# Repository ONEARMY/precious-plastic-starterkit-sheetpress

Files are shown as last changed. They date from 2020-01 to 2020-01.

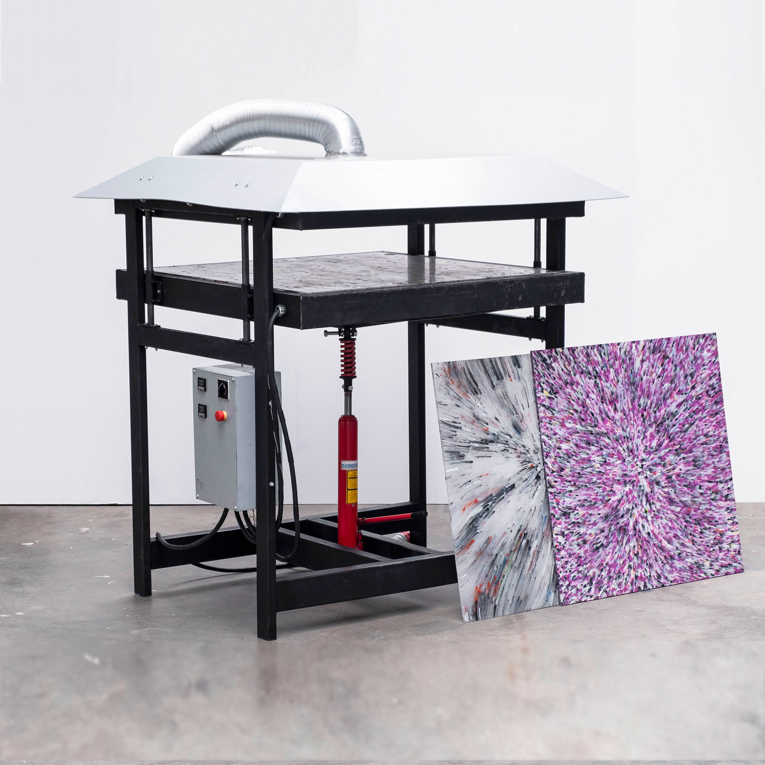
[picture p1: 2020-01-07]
3. Build the machine/Sheetpress-image.jpg

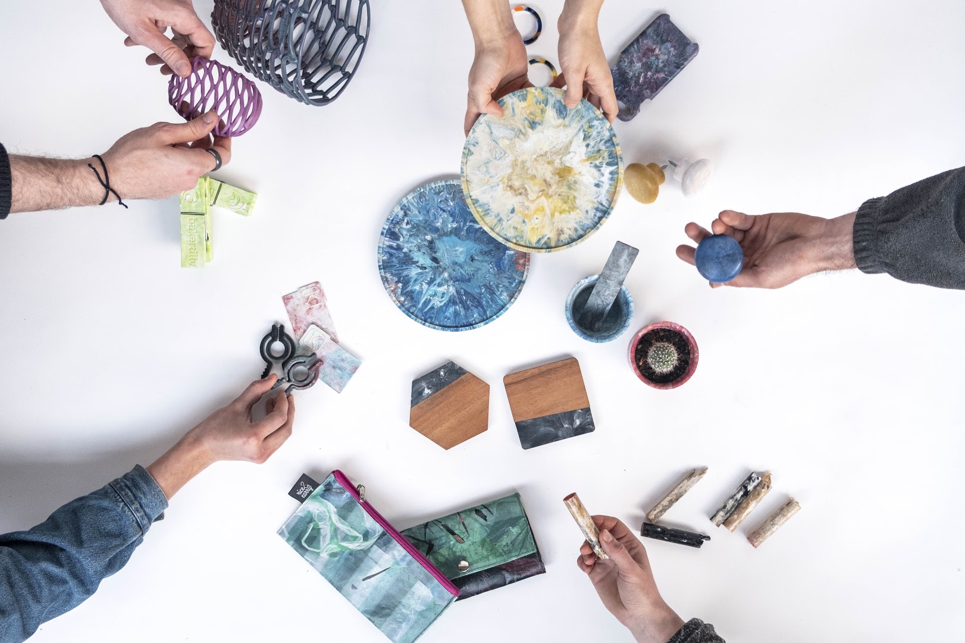
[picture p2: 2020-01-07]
6. Run your Workspace/3. Share/2. Project Images/Products/Products.jpg

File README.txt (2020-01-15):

# Starterkit - Sheetpress Workspace V1.1

YEAH, you made it into a starter-kit!
Start with the 0. Start folder.. read the introduction text and make sure to watch the videos from our website.

If you have any questions visit our community platform or Discord
https://community.preciousplastic.com/
https://discordapp.com/invite/rnx7m4t

Good luck!!

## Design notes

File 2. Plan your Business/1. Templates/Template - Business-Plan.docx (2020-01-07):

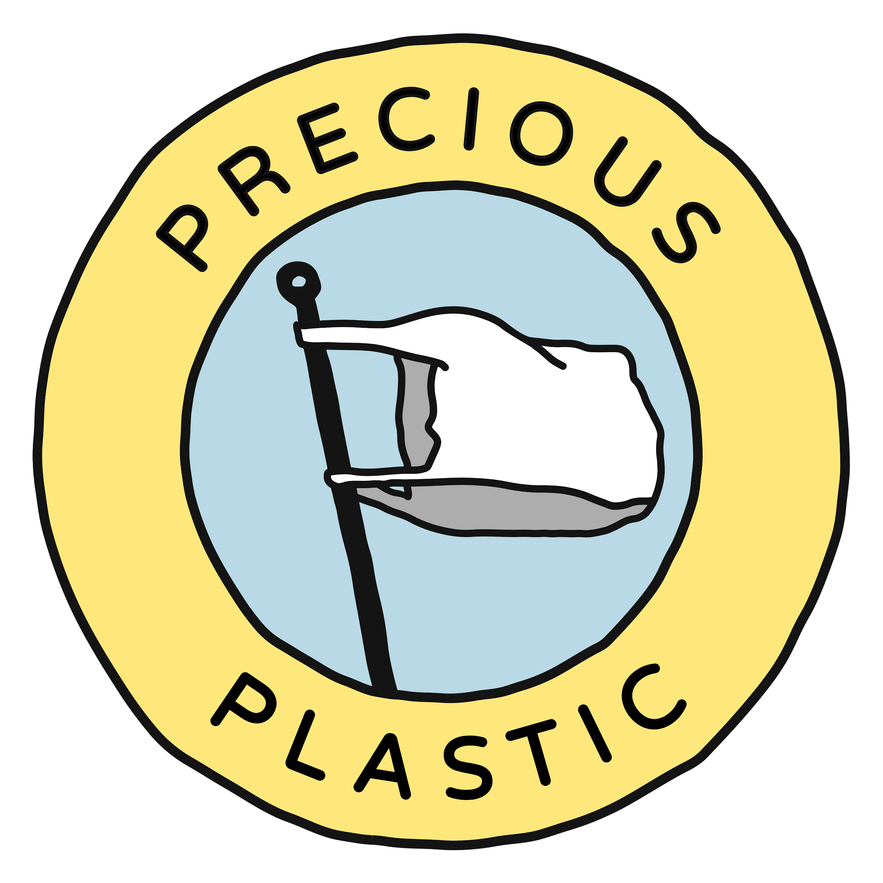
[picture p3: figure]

Your Logo and Business Name Here 👆

# Contact Details

Contact name:

Address:

City:

Zip:

Email:

Phone Number:

Website URL :

# Outline

1. Executive summary
2. Mission
3. Team
4. Market Analysis
  a. Product and Services
  b. Target Groups
  c. Engagement
  d. Sales Channels
5. Operations
  a. Key Resources
  b. Key Activities
  c. Running Costs
  d. Collaborators
6. Impact Measures
  a. Community
  b. Planet
  c. Income Streams
7. Financials
8. Legal Structure
9. Appendix

# 1. Executive Summary

This is your chance to quickly make your argument of what the problem is and how your business is going to solve it. This section shouldn’t be more than a couple paragraphs. Quickly cover the problem, your unique solution, who you’re targeting, and what your impact will be. It’s best to write this section after you’ve completed the whole business plan.

# 2. Mission

What’s the problem?

It’s best to start off describing what problem you’re solving. If your audience might need some education about the plastic waste problem - here’s your chance. What part or aspect of the plastic waste problem are you focusing on? You can set some context about the global plastic waste issue, but make sure to drill down to your national and local level as well. Try to be specific and stress why this is such a big problem facing the planet and your local community. Show your passion for solving this problem. This section will set the stage for the whole story told throughout the plan.

What’s your solution?

Next briefly cover how your solution addresses this problem. For example, if you write about how the plastic waste problem is due to a lifestyle issue, maybe you’re solution is focused on educating people because it addresses the root cause of the problem.

What’s your mission statement?

Look back on your mission that you filled out in the action plan. How can you elaborate to explain it to your reader?

What’s your vision?

Once you have explained your mission - write just a few sentences about your vision. What kind of world do you envision, and what do you envision for your organization?

# 3. Team

Fill in some basic information about your team to show who’s involved and what relevant skills and experience they have to the business.

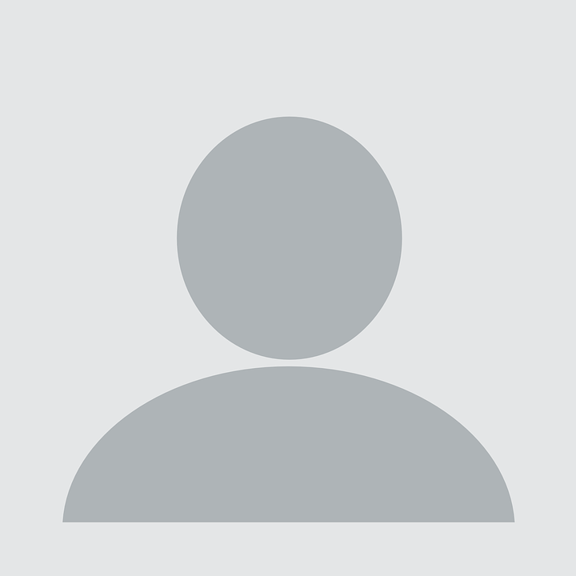
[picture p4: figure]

Name: Role: Experience: | Name: Role: Experience: | Name: Role: Experience:

# 4. Market Analysis

The market analysis section (broken down by the right side of the action plan), is where you will describe how the market is currently performing in your area of interest, how you plan to enter the market, what makes you different, who you are targeting, and how you will deliver your products and services to the customer.

## A. Products & Services

Product explanation

Explain that there is something missing from the market currently and what unique products or services you will offer to meet that unmet need. Write down a brief description of the products and services you are planning to make and include some pictures if possible. Include the price range they will be in and how this compares to similar products/services. If you have any sketches or pictures of your products, you can also include them here.

Product Photos or Sketches:

Competitive advantage

It’s unlikely that your product or service is completely unique - there are businesses or organizations that are probably doing something similar. What are those businesses, what are they offering, and how are you differentiating yourself? Another way to ask this what is your competitive advantage? What are you doing that sets you apart? Describe it here.

Total Available Market

What would you estimate to be the total available market for your product or service? For example, I’m targeting the plastic waste generated in my town, and I know from my city waste department that we generate about 100 tons per month of waste plastic. That means if we were to capture 100 % of the market, we would be processing all 100 tons. If we value each ton at $10, that a $12,000 total available market per year. You should include the total available market that you’re targeting to show how big your business could potentially grow.

## B. Target Groups

Identify the groups

In this section, explain who your target customer groups are, and how many potential customers are in this group. What do you know about these groups? This is your chance to communicate your research about your customers.

Research

What research have you done to show that your target groups will be interested in your products and services? Discuss any field research that you’ve done or online research about these groups. For example, if you’re producing craft furniture from plastic waste, do some research online to see if you can find numbers on the total craft furniture market value in your country. You could also run a small survey in your area to gauge interest in your products.

If you’re targeting businesses, do you have any letters of intent or proof that they are willing to buy your product or service when you’re able to get up and running? This can be a very powerful tool for showing your business case - you already have customers lining up to buy.

## C. Engagement

Engagement is how you will engage with your target customer groups and how many people you can potentially reach with this engagement strategy. What marketing channels are you using? If you’re using social media - which platforms? What’s your engagement rollout plan? Do you intend to start with one marketing channel and then gradually expand? Communicate your marketing plan here.

## D. Sales Channels

Finally, explain what your sales channels are. Explain where and how people can buy your products/services. Explain why you chose these sales channels, and relate that back to your target groups.

Business to Business (B to B) versus Business to Consumer (B to C)

Are you focusing on business to consumer or business to business? This is an important distinction, because it will help the reader understand your business model. Business to consumer (B to C) means that you are targeting consumers directly - you will be the one selling the product or service to the end user. If you are instead focusing on business to business (B to B), that means that you’ll be selling to other businesses. For example - if you’re a machine builder that will be selling machines to new workspaces - this is a business to business model. If you are a product producer selling products directly to people through the Precious Plastic Bazar, this is an example of business to consumer.

# 5. Operations

## A. Key Resources

First explain what key resources, or the key tools, machines, people, and any other resources that are crucial for you to deliver on your mission.

Another good thing to include here is any permits or licenses that you might need from the government in order to be able to operate. Are there any safety requirements that you need to follow? What resources do you need to have available in order to do so? What about people - are there any key skill sets that you need?

Include any pictures of your workspace if it’s relevant as well.

## B. Key Tasks

Explain your key tasks - What actions and activities will you need to focus on? Show that you have a clear sense of what needs to be done. How will produce your product or service and what are the key tasks that you must do to support this core delivery. Describe your production or service delivery process in detail and how you will maintain quality. How do you and your team’s skills and experience match up with these activities?

## C. Running Costs

In this section you will describe in more detail the key running costs that you identified in the Action Plan. Doesn’t need to be very long - this is just to show that you’ve thought about the costs that are a risk to the business month after month. If you have a way to control these costs, discuss that here as well.

## D. Collaborators

Finally, write about who your key collaborators are. What people, groups and organizations will be key in helping you fulfill your mission? Say what they will add to your business, and what your current relationship is with them. Are these people you would like to collaborate with, or you’ve already started? What’s the current status? How will they help you deliver on your mission? Be specific here - show what strategic relationships that you have which will be a strategic asset to your business.

# 6. Impacts

## A. Community

Here’s your chance to write about the positive impact you will have on your community. What’s the direct impact you will have on improving the lives of real people? Link this back to your mission and vision if possible.

You can also discuss your involvement with the Precious Plastic community. Perhaps discuss how you will contribute back to the Precious Plastic open source community and share your knowledge with other Precious Plastic workspaces.

## B. Planet

The planet section is for you to discuss the positive impact you will have on the environment. Show your vision and dream about a cleaner, greener future. It’s important to think about how you will measure this as well. For many Precious Plastic businesses this will be the amount of material recycled.

## C. Income Streams

Next describe your revenue model, or how you intend to bring in money month after month. Refer back to what you wrote in the action plan - is it product sales, workshop ticket sales, machine maintenance fees, or some other revenue model? How do you intend to price your products and services? Do you have different models for different products and services? Describe each one in detail.

# 7. Financials

The financials section is where you will build holistic financial picture to argue that you can turn your idea into a financially successful business.

First, write about the investment costs that you will have to pay in order to get started. You can pull this information from the workspace calculator and paste into a table. Copy in the investment costs table from the workspace calculator and add a total value.

Investment Costs
Initial Investments | Cost
Total:

Next describe how you intend to raise the initial money you need to get started. Is this a bank loan, grants, your private money, or assistance from the local government? Describe the different forms of financial assistance that you are pursuing.

Next you should copy in the Profit & Loss statement from the workspace calculator generated on the “extras” page. The profit and loss statement shows your estimated financial outlook for the first three years of operation.

Profit and Loss Statement
| Year 1 | Year 2 | Year 3
Revenue
Cost of Sales
Net Revenue
Fixed Costs
Gross Income from Operations
Business Taxes
Net Income

The cash flow statement shows that you will have enough money on hand to meet your financial obligations throughout the first year. Grants or bank loan applications often ask for these statements.

Cash Flow Statement
Month
Money In Bank (Beginning of Month)
Initial Investment
Revenue
Total Cash In
Investment Costs
Variable Costs
Fixed Costs
Total Cash Out
Net Cash Flow
Money In Bank (End of Month)

8. Legal Structure

The legal structure section is where to describe how you’ll be organized as a legal entity, or how you’re registered with the government. Your project doesn’t need to be structured as a commercial business - could be a non-profit, association, cooperative, project within an existing business, B - corp, social business. “Business plan” is the terminology that’s often used for a plan such as this, but doesn’t mean you need to run it necessarily as a “for-profit” business. This is going to depend on your situation, and could also depend on your country - sometimes it’s easier to structure a project a certain way depending on the legal entity regulations. One or the other maybe more tax friendly - more often a non-for profit or association is the more favorable tax structure for receiving grants. Describe here which legal structure you intend to use and why.

# 9. Appendix

The appendix is the place at the end of your business plan for any other supporting documents, pictures, graphs, or anything else you can think of that will help build your case. You can refer to items in the appendix throughout your document. Some items that could be found here are signed letters of intent from businesses wanting to buy your product, extra pictures of your products or services, additional financial graphs, and letters of understanding between you and collaborators.

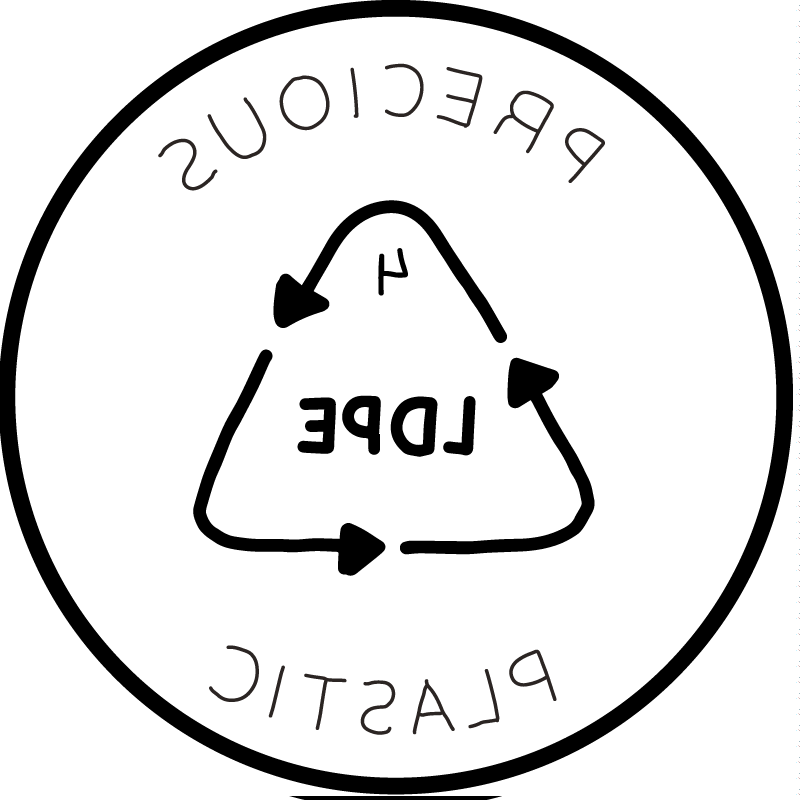
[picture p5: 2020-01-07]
6. Run your Workspace/1. Plastic Type Stamps/Stamps/LDPE.png

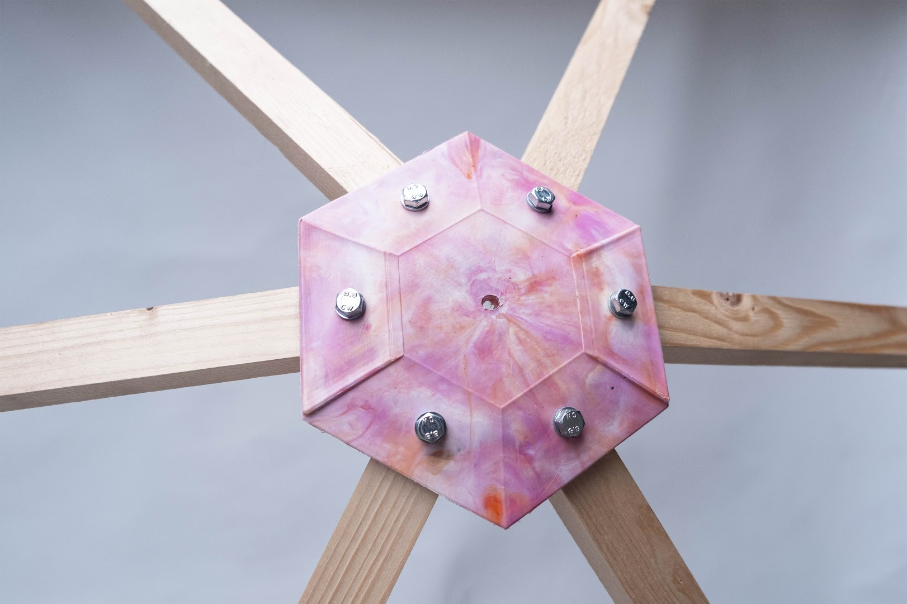
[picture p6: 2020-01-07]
6. Run your Workspace/3. Share/2. Project Images/Products/Dome-Close.jpg

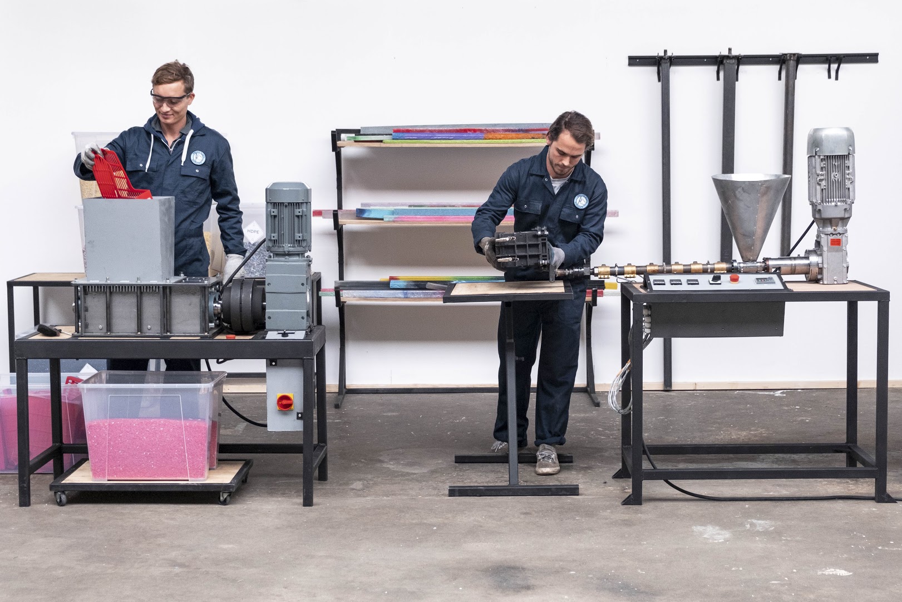
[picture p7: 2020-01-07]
6. Run your Workspace/3. Share/2. Project Images/At Work/Shreddier-and-Extrusion.jpg

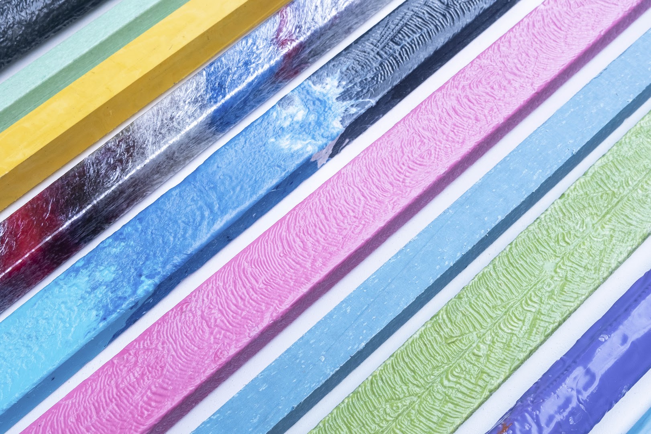
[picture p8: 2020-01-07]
6. Run your Workspace/3. Share/2. Project Images/Products/Beams.jpg

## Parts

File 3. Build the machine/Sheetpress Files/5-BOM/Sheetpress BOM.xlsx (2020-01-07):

Type | Item | Qty. | URL (Europe) | Price | Part/Assembly Number | Notes
Beams and Sheets | 150mm x 3000mm x 1.5m Sheet Steel | 1 | https://www.danielsmetalen.nl/prijslijst_constructiestalen_plaatmaterialen.pdf#page=1 | €48.60 | SPR-V1 2000.01-A, SPR-V1 3000.01-A
Beams and Sheets | 2449mm x 1220mm x 3m Plywood | 1 | https://www.hornbach.nl/shop/Multiplexplaat-Powerplex-Pure-interieur-2440-x-1220-x-3-6-mm/8492350/artikel.html | €15.29 | SPR-V1 0000.02-A
Beams and Sheets | 2mm Sheet Steel Laser Cut | 1 | https://www.247tailorsteel.com | €47.04 | SPR-V1 5000.01-A, SPR-V1 5000.02-A
Beams and Sheets | 27mm Steel Tube Stock 6m | 1 | https://www.danielsmetalen.nl/prijslijst_constructiestalen_plaatmaterialen.pdf#page=1 | €40 | SPR-V1 1000.03-A, SPR-V1 4000.02-A | Special Order from supplier. Should run smooth inside of eachother. You can use the same tubes you used for the Injection machine.
Beams and Sheets | 36mm x 4mm Steel Tube Extrsion 6m | 1 | https://www.danielsmetalen.nl/prijslijst_constructiestalen_plaatmaterialen.pdf#page=1 | €14 | SPR-V1 1000.02-A, SPR-V1 4000.01-A
Beams and Sheets | 6mm Sheet Steel Laser Cut | 1 | https://www.247tailorsteel.com | €407.53 | SPR-V1 0000.01-A, SPR-V1 0000.03-A, SPR-V1 0000.03-A, SPR-V1 1000.02-A, SPR-V1 1000.02-A, SPR-V1 1000.04-A, SPR-V1 1000.05-A, SPR-V1 2100.03-A, SPR-V1 2100.04-A, SPR-V1 2100.05-A, SPR-V1 3100.03-A, SPR-V1 3100.04-A, SPR-V1 3100.05-A, SPR-V1 4000.01-A, SPR-V1 4000.02-A SPR-V1 5000.01-A
Beams and Sheets | 10mm Milled Aluminium Sheet | 2 | https://gleich.de/us/products/g-al-c250/ | €500 | SPR-V1 2100.02-A, SPR-V1 3100.02-A
Beams and Sheets | 40mm x 80mm Box Extrusion 6m | 2 | https://www.danielsmetalen.nl/prijslijst_constructiestalen_plaatmaterialen.pdf#page=1 | €53.90 | SPR-V1 1000.01-A
Beams and Sheets | 120mm x 60mm Box Extrusion 6m | 3 | https://www.danielsmetalen.nl/prijslijst_constructiestalen_plaatmaterialen.pdf#page=1 | €128.61 | SPR-V1 0000.01-A, SPR-V1 2100.01-A, SPR-V1 3100.01-A
Beams and Sheets | 25mm x 50mm Aluminum Stock 1.2m | 4 | https://gleich.de/us/products/en-aw-5083/ | €100 | SPR-V1 3000.02-A
Fastners | M6 x 12mm Button Head Bolt | 28 | https://www.fabory.com/en_NL/hexagon-socket-button-head-screw-iso-7380-1-steel-plain-010-9/p/07150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 | €1.70 | SPR-V1 10
Fastners | M6 Washer Large | 28 | https://www.fabory.com/en_NL/plain-washer-type-ll-nf-e25-513-steel-plain/p/38073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 | €0.86 | SPR-V1 11
Fastners | M8 x 50 Countersunk Bolt | 118 | https://www.fabory.com/en_NL/hexagon-socket-countersunk-head-screw-din-%e2%89%887991-steel-plain-08-8/p/07465 | €31.85 | SPR-V1 13
Fastners | M8 x 100 Hex Bolt | 26 | https://www.fabory.com/en_NL/hexagon-head-screw-din-933-steel-plain-8-8-din-933/p/01010 | €6.61 | SPR-V1 07
Fastners | M8 Nut | 152 | https://www.fabory.com/en_NL/hexagon-nut-din-934-steel-plain-%7c10%7c/p/04120?q=%3Arelevance%3AFA5500%3ASteel | €13.17 | SPR-V1 08
Fastners | M8 Washer | 122 | https://www.fabory.com/en_NL/plain-washer-din-125-1a-steel-140hv-plain/p/38100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 | €1.48 | SPR-V1 09
Fastners | M16x120 Hex Bolt | 3 | https://www.fabory.com/en_NL/hexagon-head-bolt-mf-din-960-steel-plain-8-8-din-960/p/01060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 | €6.30 | SPR-V1 04
Fastners | M16x140 Hex Bolt | 6 | https://www.fabory.com/en_NL/hexagon-head-bolt-mf-din-960-steel-plain-8-8-din-960/p/01060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 | €14.64 | SPR-V1 03
Fastners | M16 Nut | 16 | https://www.fabory.com/en_NL/hexagon-nut-din-934-steel-plain-%7c10%7c/p/04120?q=%3Arelevance%3AFA5500%3ASteel | €4.64 | SPR-V1 05
Fastners | M16 Washer | 12 | https://www.fabory.com/en_NL/plain-washer-type-l-nf-e25-513-steel-zinc-plated-yellow-passivated/p/38067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 | €2.28 | SPR-V1 06
Electronics | 1/4" PTFE Shrink Wrap | 3.6m | https://www.ebay.nl/itm/TFER-High-Temperature-Heat-Shrink-PTFE-TE-Connectivity-Raychem-Clear-3-2-1/254073249059 | €36.66 | SPR-V1 2000.00-A, SPR-V1 3000.00-A, SPR-V1 5000.00-A
Electronics | 1/8" PTFE Shrink Wrap | 3.6m | https://www.ebay.nl/itm/TFER-High-Temperature-Heat-Shrink-PTFE-TE-Connectivity-Raychem-Clear-3-2-1/254073249059 | €38.75 | SPR-V1 2000.00-A, SPR-V1 3000.00-A, SPR-V1 5000.00-A
Electronics | 300W 12x80mm Cartridge Heater | 49 | https://nl.aliexpress.com/item/32867272365.html | €240.30 | SPR-V1 2100.00-A, SPR-V1 3000.00-A,
Electronics | 32A Ceramic Terminal | 8 | https://www.ebay.com/itm/3-Way-57A-450V-Ceramic-Terminal-Block-Connector-Steatite-High-Temperature/302836663974 | €25.86 | SPR-V1 2100.00-A, SPR-V1 3000.00-A
Electronics | 32A Circuit Breaker Relay | 2 | https://www.distrelec.nl/en/contactor-1nc-3no-230v-32a-15kw-eaton-dilm32-01-230v50-60hz/p/30129499?track=true | €151.40 | SPR-V1 2000.00-A, SPR-V1 3000.00-A, SPR-V1 5000.00-A
Electronics | 32A Male Plug | 1 | https://www.hornbach.nl/shop/PCE-CEE-Fase-inverter-32A/828922/artikel.html | €12.50 | SPR-V1 5000.00-A
Electronics | 40A SSR | 2 | https://www.amazon.de/KKmoon-24V-380V-SSR-40-Relaismodul-Temperaturregler/dp/B010Q6898C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 | €17.98 | SPR-V1 5000.00-A
Electronics | Emergency Stop | 1 | https://www.distrelec.nl/en/emergency-stop-switch-1nc-ip20-connection-box-ip65-front-panel-idec-yw1b-v4e01r/p/30102672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 | €9.25 | SPR-V1 5000.00-A
Electronics | Fork Terminal Blue | 100 | https://www.distrelec.nl/en/insulated-fork-terminal-blue-mm-pack-of-100-pieces-rnd-connect-rnd-465-00662/p/30110440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 | €3.83 | SPR-V1 5000.00-A
Electronics | Fork Terminal Red | 100 | https://www.distrelec.nl/en/insulated-fork-terminal-red-mm-pack-of-100-pieces-rnd-connect-rnd-465-00660/p/30110438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 | €4.21 | SPR-V1 5000.00-A
Electronics | H07 5 Multi-core Cable (6mm) | 20 | https://www.neopreen-kabel.nl/5-aderige-neopreenkabel/24-5-x-25-mm2-neopreenkabel-tm-99-meter.html | €56.27 | SPR-V1 5000.00-A
Electronics | Heat Resistant Wire | 50m | https://www.ebay.com/itm/OVENS-COOKERS-GANTRY-LAMPS-HIGH-TEMPERATURE-ELEMENT-WIRE-CABLE-WIRING-1-5mm/140518694383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 | €86.89 | SPR-V1 2000.00-A, SPR-V1 3000.00-A, SPR-V1 5000.00-A
Electronics | K Type Thermocouple | 2 | https://www.amazon.de/Keenso-Thermoelementsensoren-M8-Gewinde-Typ-K-Sensor-Hochtemperatur-Thermoelement/dp/B07RBKT2S4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 | €14.98 | SPR-V1 2000.00-A, SPR-V1 3000.00-A, SPR-V1 5000.00-A
Electronics | M10 Cable Gland | 1 | https://www.amazon.de/sourcingmap%C2%AE-Steckverbinder-Befestigung-Locknut-Stuffing/dp/B072J25M8Y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 | €11.79 | SPR-V1 14
Electronics | M25 Cable Gland | 5 | https://www.amazon.de/dp/B00GO4Q8KW?s=diy | €24.40 | SPR-V1 2000.00-A, SPR-V1 3000.00-A, SPR-V1 5000.00-A
Electronics | PID Controller | 2 | https://www.amazon.de/Digitaler-Temperaturregler-REX-C100-Thermostat-Relaisausgang/dp/B078M7GCDK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 | €13.49 | SPR-V1 5000.00-A
Electronics | Ring Terminal | 6 | https://www.distrelec.nl/en/ring-cable-lug-yellow-mm-pvc-te-connectivity-160292/p/14820858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 | €1.98 | SPR-V1 2000.00-A, SPR-V1 3000.00-A, SPR-V1 5000.00-A
Electronics | Rotary Switch | 1 | https://www.distrelec.nl/en/cam-switch-poles-positions-baco-pr-12-1101-a4-q48pn/p/13511954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 | €15.51 | SPR-V1 5000.00-A
Electronics | SSR Heatsink | 2 | https://www.amazon.de/easycargo-Aluminium-K%C3%BChlk%C3%B6rper-Heizk%C3%B6rper-80-mmx50mmx50/dp/B07B3Y2ZNY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 | €19.98 | SPR-V1 5000.00-A
Misc. | 8 Ton Long Ram Pin Mount Jack | 1 | https://www.kippersrijssen.nl/werkplaatsinrichting/uitdeuksets/lange-cilinder-8-ton | €54.45 | SPR-V1 01 | 28mm Ram
Misc. | Black Heat Resitant Metal Paint | 20 | https://www.action.com/nl-nl/p/spectrum-matte-hittebestendige-spuitverf/ | €59.80 | SPR-V1 0000.01-A, SPR-V1 0000.03-A, SPR-V1 1000.01-A, SPR-V1 1000.02-A, SPR-V1 1000.04-A, SPR-V1 1000.05-A, SPR-V1 2100.01-A, SPR-V1 2100.03-A, SPR-V1 2100.05-A, SPR-V1 3100.01-A, SPR-V1 3100.03-A, SPR-V1 3100.04-A, SPR-V1 3100.05-A, SPR-V1 4000.01-A, SPR-V1 4000.02-A,
Misc. | Fibreglass tape | 2 | https://www.hornbach.nl/shop/KNAUF-Easytape-zelfklevend-wapeningsband-breedte-48-mm-rol-20-mtr/5098616/artikel.html | €2.90 | SPR-V1 0000.02-A
Misc. | Grey Metal Paint | 1 | https://www.gamma.nl/assortiment/gamma-metaallak-grijs-500-ml/p/B825931 | €18.95 | SPR-V1 0000.02-A, SPR-V1 2000.01-A, SPR-V1 3000.01-A, SPR-V1 5000.01-A, SPR-V1 5000.02-A
Misc. | Hardener | 2 | https://www.hornbach.nl/shop/ALABASTINE-Polyesterplamuur-harder-30-gr/4193261/artikel.html | €5.29 | SPR-V1 0000.02-A
Misc. | Heat Conductive Putty | 1 | https://www.briskheat.com/heat-conductive-putty-hcp.html | €89.00 | SPR-V1 2000.00-A, SPR-V1 3000.00-A
Misc. | Hose Clamp | 1 | https://www.hornbach.nl/shop/ROTHEIGNER-Slangklem-60-165-mm-2-stuks/8218147/artikel.html | €3.55 | SPR-V1 0000.00-A
Misc. | Hose Connector | 1 | https://www.hornbach.nl/shop/ROTHEIGNER-Muuraansluitplaat-rond-kunststof-wit-150-mm/8610894/artikel.html | €8.95 | SPR-V1 02
Misc. | Resin | 2 | https://www.hornbach.nl/shop/ALABASTINE-Polyester-hars-500-ml/4139114/artikel.html | €13.49 | SPR-V1 0000.02-A
Misc. | Rock Wool | 2 | https://www.gamma.nl/assortiment/rockwool-rocksono-solid-70-mm-3-6-m2-rd-1-90/p/B399898?gclsrc=aw.ds | €13.98 | SPR-V1 2000.00-A, SPR-V1 3000.00-A
Misc. | Spring | 1 | https://www.berger-tools.co.uk/Die_Springs_Iso_European_Standard/R__Red_Die_Spring_Iso10243__Heavy_Load/ | €51.10 | SPR-V1 15 | R63-152
Misc. | White Primer |  | https://www.gamma.nl/assortiment/ok-binnenlak-grondverf-1-l-wit/p/B107965 | €9.00 | SPR-V1 0000.02-A
 |  |  | Total: | €2554.99

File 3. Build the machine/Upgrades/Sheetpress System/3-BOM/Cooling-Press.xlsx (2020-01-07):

Type | Item | Qty. | URL (Europe) | Price | Notes
Beams and Sheets | 2449 x 1220 x 12-18mm Plywood | 1 | https://www.hornbach.nl/shop/Multiplexplaat-Powerplex-Pure-interieur-2440-x-1220-x-18-mm/8492345/artikel.html | €48.99
Beams and Sheets | 27mm ø Steel Tube Stock 6m | 1 | https://www.danielsmetalen.nl/prijslijst_constructiestalen_plaatmaterialen.pdf#page=1 | €40 | Special Order from supplier. Should run smooth inside of eachother. Possible to use leftover from Sheetpress. You can use the same tubes you used for the Injection machine .
Beams and Sheets | 36 x 4 Steel Tube Extrsion 6m | 1 | https://www.danielsmetalen.nl/prijslijst_constructiestalen_plaatmaterialen.pdf#page=1 | €14
Beams and Sheets | 40 x 40 Box Extrusion 6m | 2 | https://www.danielsmetalen.nl/prijslijst_constructiestalen_plaatmaterialen.pdf#page=1 | €33.12
Beams and Sheets | 40 x 80 Box Extrusion 6m | 3 | https://www.danielsmetalen.nl/prijslijst_constructiestalen_plaatmaterialen.pdf#page=1 | €80.85
Beams and Sheets | 6mm Sheet Steel Plasma Cut |  | https://www.247tailorsteel.com | €300.00
Fastners | M8 x 100 Hex Bolt | 8 | https://www.fabory.com/en_NL/hexagon-head-screw-din-933-steel-plain-8-8-din-933/p/01010 | €0.97 | You can use leftover from Sheetpress
Fastners | M8 Nut | 16 | https://www.fabory.com/en_NL/hexagon-nut-din-934-steel-plain-%7c10%7c/p/04120?q=%3Arelevance%3AFA5500%3ASteel | €1.38
Fastners | M8 Washer | 8 | https://www.fabory.com/en_NL/plain-washer-din-125-1a-steel-140hv-plain/p/38100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 | €0.09
Fastners | M16x120 Hex Bolt | 8 | https://www.fabory.com/en_NL/hexagon-head-bolt-mf-din-960-steel-plain-8-8-din-960/p/01060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 | €16.80
Fastners | M16 Nut | 10 | https://www.fabory.com/en_NL/hexagon-nut-din-934-steel-plain-%7c10%7c/p/04120?q=%3Arelevance%3AFA5500%3ASteel | €2.90
Fastners | M16 Washer | 12 | https://www.fabory.com/en_NL/plain-washer-type-l-nf-e25-513-steel-zinc-plated-yellow-passivated/p/38067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 | €2.28
Misc. | 3 Ton Long Ram Pin Mount Jack | 1 | https://www.barntools.nl/hydraulische-cilinder-3-ton-enkel-62-cm.html | €45.00
Misc. | Black Heat Resitant Metal Paint | 20 | https://www.action.com/nl-nl/p/spectrum-matte-hittebestendige-spuitverf/ | €59.80
 |  |  | Total: | €646.18
 |  |  | Total: | €1292.36

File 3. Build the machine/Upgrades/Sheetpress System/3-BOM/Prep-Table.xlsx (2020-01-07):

Type | Item | Qty. | URL (Europe) | Price | Notes
Beams and Sheets | 2449 x 1220 x 12-18mm Plywood | 1 | https://www.hornbach.nl/shop/Multiplexplaat-Powerplex-Pure-interieur-2440-x-1220-x-18-mm/8492345/artikel.html | €48.99
Beams and Sheets | 40 x 40 Box Extrusion 6m | 3 | https://www.danielsmetalen.nl/prijslijst_constructiestalen_plaatmaterialen.pdf#page=1 | €49.68
Beams and Sheets | 6mm Sheet Steel Plasma Cut |  | https://www.247tailorsteel.com | €40.00
Fastners | M6 x 12mm Button Head Bolt | 16 | https://www.fabory.com/en_NL/hexagon-socket-button-head-screw-iso-7380-1-steel-plain-010-9/p/07150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 | €0.97 | You can use leftover from Sheetpress
Fastners | M8 x 100 Hex Bolt | 4 | https://www.fabory.com/en_NL/hexagon-head-screw-din-933-steel-plain-8-8-din-933/p/01010 | €1.01
Fastners | M8 Nut | 4 | https://www.fabory.com/en_NL/hexagon-nut-din-934-steel-plain-%7c10%7c/p/04120?q=%3Arelevance%3AFA5500%3ASteel | €0.34
Fastners | M8 Washer | 4 | https://www.fabory.com/en_NL/plain-washer-din-125-1a-steel-140hv-plain/p/38100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 | €0.04
Misc. | Caster Wheels | 4 | https://www.gamma.nl/assortiment/dubbel-zwenkwiel-rem-met-plaat-maximaal-80-kg-50-mm/p/B624670 | €51.96
Misc. | Black Heat Resitant Metal Paint | 5 | https://www.action.com/nl-nl/p/spectrum-matte-hittebestendige-spuitverf/ | €14.95
 |  |  | Total: | €207.94

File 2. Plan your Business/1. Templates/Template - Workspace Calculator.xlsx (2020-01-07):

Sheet: Read Me!
Precious Plastic Workspace Calculator
 | Welcome to the Precious Plastic Workspace Calculator! This tool will help you understand the numbers behind starting a Precious Plastic business.
You will learn:
- How much money you need to start your workspace
- How long it will take to pay back your intitial investment
- What prices for your products will cover the costs of production
Before you get started:
1. Only fill in cells that are bordered in blue
2. Get started by clicking on the sales tab below
 |  | Cells where you should enter numbers
 |  | Cells with numbers we calculate for you
 |  | If you click cells with red arrows, more information pops up

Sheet: 1. Sales
Sales
In the first column, list all the products, machines, workshops or services that you plan on selling with your Precious Plastic workspace. In the second column, estimate how much each product or service would cost you in materials. In the third column, estimate the time it will take to create each product or service.
Products or Services | Material Cost for Each Product | Number of Working Hours to Produce Each Product or Service

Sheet: 2. Costs
Working Hours |  | Investment Costs |  | Fixed Costs
Besides making products & services, you will have to spend time on doing other tasks. In this section, fill in your weekly activities and how many hours you will spend on each activity per week. Do not include the time to directly produce products or services. |  | These are the machines, tools, and other expenses you need to set up your workspace. These costs are also known as your "investment costs" and are only paid once. |  | Fixed costs are the costs that do not vary with the amount of products and services that you produce, but you have to pay on a regular basis. Some costs may need to be paid quarterly or yearly, so do some quick calculations to estimate them on a monthly basis.
Weekly Activities | Hours per Week | Initial Investments | Cost | Fixed Costs | Cost per Month

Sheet: 3. Dashboard
Dashboard | Sales Overview |  |  |  |  | Wages
 | Products & Services | Selling Price Per Unit | Number of Expected Sales Per Month | Total Product Cost | Profit Margin | Hourly Wage
Start by entering your desired hourly wage, selling prices, and expected sales for each product. Then play around with your pricing, hourly wage, and expected sales to see how it affects the time needed to pay back your investment, monthly profit, and monthly pay. Make sure you set prices for your products and services so that the numbers in the profit margin column turn green, which means you are covering the costs of producing them. |  |  |  |  |  |  | 3 | *
 |  |  |  |  |  | Summary
 |  |  |  |  |  | Money Needed to Start
 |  |  |  |  |  | Months to Pay Back Investment | Too Long!
 |  |  |  |  |  | Full Time Employees Needed | 0.0
 |  |  |  |  |  | Revenue Earned Per Month | 0.00
 |  |  |  |  |  | Fixed Costs Per Month | 0.00
 |  |  |  |  |  | Material Costs Per Month | 0.00
 |  |  |  |  |  | Total Wages Paid Per Month | 0.00
 |  |  |  |  |  | Total Profit Earned Per Month | 0

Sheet: Extras
Extras
This page provides you with some basic finanial statements (Cashflow and Profit & Loss) and shows you the calculations from the previous pages. It's more for those people who want to dive deep into the numbers or provide a bank with forecasted financial statements.
Cash Flow A cash flow analysis shows that you have enough money throughout your first year to buy materials, pay your employees, or make an investment into a new machine.
 | Month 1 | Month 2 | Month 3 | Month 4 | Month 5 | Month 6 | Month 7 | Month 8 | Month 9 | Month 10 | Month 11 | Month 12
Money In Bank (Beginning of Month) |  | 0.00 | 0.00 | 0.00 | 0.00 | 0.00 | 0.00 | 0.00 | 0.00 | 0.00 | 0.00 | 0.00
Initial Investment
Revenue | 0.00 | 0.00 | 0.00 | 0.00 | 0.00 | 0.00 | 0.00 | 0.00 | 0.00 | 0.00 | 0.00 | 0.00
Total Cash In | 0.00 | 0.00 | 0.00 | 0.00 | 0.00 | 0.00 | 0.00 | 0.00 | 0.00 | 0.00 | 0.00 | 0.00
Investment Costs | 0.00
Variable Costs | 0.00 | 0.00 | 0.00 | 0.00 | 0.00 | 0.00 | 0.00 | 0.00 | 0.00 | 0.00 | 0.00 | 0.00
Fixed Costs | 0.00 | 0.00 | 0.00 | 0.00 | 0.00 | 0.00 | 0.00 | 0.00 | 0.00 | 0.00 | 0.00 | 0.00
Total Cash Out | 0.00 | 0.00 | 0.00 | 0.00 | 0.00 | 0.00 | 0.00 | 0.00 | 0.00 | 0.00 | 0.00 | 0.00
Net Cashflow | 0.00 | 0.00 | 0.00 | 0.00 | 0.00 | 0.00 | 0.00 | 0.00 | 0.00 | 0.00 | 0.00 | 0.00
Money In Bank (End of Month) | 0.00 | 0.00 | 0.00 | 0.00 | 0.00 | 0.00 | 0.00 | 0.00 | 0.00 | 0.00 | 0.00 | 0.00
Profit and Loss This table is to show how much money the company is projected to make each year. It assumes that you paid yourself for the hours you worked, so the "Net Income" at the bottom is the remaining profit made by your company. It is greatly influenced by the "Monthly Sales Improvement Rate" on the Dashboard page. This table is also useful to show your bank or include in grant applications.
 | Year 1 | Year 2 | Year 3 |  | Yearly Growth Rate
Revenue | 0.00 | 0.00 | 0.00 |  | Low
Cost of Sales | 0.00 | 0.00 | 0.00 |  | 0.10 €
Net Revenue | 0.00 | 0.00 | 0.00
Fixed Costs | 0.00 | 0.00 | 0.00
Gross Income from Operations | 0.00 | 0.00 | 0.00
 |  |  |  |  | Business Tax Rate (Research for your Country)
Business Taxes | 0.00 | 0.00 | 0.00 |  | 20.00%
Net Income | 0.00 | 0.00 | 0.00
Monthly Sales Figures
Products and Services | Revenue | Overhead Cost | Indirect Labor Cost | Production Labor Cost | Material Cost | Total Monthly Cost | Total Monthly Profit | Total Monthly Hours
 |  |  |  |  |  |  | #VALUE! | 0.00
 |  | #DIV/0! | #DIV/0! |  |  | #DIV/0!
 |  |  |  |  |  |  | #VALUE! | 0.00
 |  | #DIV/0! | #DIV/0! |  |  | #DIV/0!
 |  |  |  |  |  |  | #VALUE! | 0.00
 |  | #DIV/0! | #DIV/0! |  |  | #DIV/0!
 |  |  |  |  |  |  | #VALUE! | 0.00
 |  | #DIV/0! | #DIV/0! |  |  | #DIV/0!
 |  |  |  |  |  |  | #VALUE! | 0.00
 |  | #DIV/0! | #DIV/0! |  |  | #DIV/0!
 |  |  |  |  |  |  | #VALUE! | 0.00
 |  | #DIV/0! | #DIV/0! |  |  | #DIV/0!
 |  |  |  |  |  |  | #VALUE! | 0.00
 |  | #DIV/0! | #DIV/0! |  |  | #DIV/0!
 |  |  |  |  |  |  | #VALUE! | 0.00
 |  | #DIV/0! | #DIV/0! |  |  | #DIV/0!
 |  |  |  |  |  |  | #VALUE! | 0.00
 |  | #DIV/0! | #DIV/0! |  |  | #DIV/0!
 |  |  |  |  |  |  | #VALUE! | 0.00
 |  | #DIV/0! | #DIV/0! |  |  | #DIV/0!
 |  |  |  |  |  |  | #VALUE! | 0.00
 |  | #DIV/0! | #DIV/0! |  |  | #DIV/0!
Total Revenue | 0.00 |  |  |  |  |  | #VALUE!
Total Cost |  | #DIV/0! | #DIV/0! | 0.00 | 0.00 | #DIV/0! |  | 0.00
Payback Table
Don't worry too much about this one, it's just to make the payback analysis graph on the dashboard | #DIV/0! | #DIV/0! | #DIV/0! | #DIV/0! | #DIV/0! | #DIV/0! | #DIV/0! | #DIV/0! | #DIV/0! | #DIV/0! | #DIV/0! | #DIV/0! | #DIV/0! | #DIV/0! | #DIV/0! | #DIV/0! | #DIV/0! | #DIV/0! | #DIV/0! | #DIV/0! | #DIV/0! | #DIV/0! | #DIV/0! | #DIV/0! | #DIV/0! | #DIV/0! | #DIV/0! | #DIV/0! | #DIV/0! | #DIV/0! | #DIV/0! | #DIV/0! | #DIV/0! | #DIV/0! | #DIV/0! | #DIV/0!
Month | 1 | 2 | 3 | 4 | 5 | 6 | 7 | 8 | 9 | 10 | 11 | 12 | 13 | 14 | 15 | 16 | 17 | 18 | 19 | 20 | 21 | 22 | 23 | 24 | 25 | 26 | 27 | 28 | 29 | 30 | 31 | 32 | 33 | 34 | 35 | 36
Money You Invested | #DIV/0! | #DIV/0! | #DIV/0! | #DIV/0! | #DIV/0! | #DIV/0! | #DIV/0! | #DIV/0! | #DIV/0! | #DIV/0! | #DIV/0! | #DIV/0! | #DIV/0! | #DIV/0! | #DIV/0! | #DIV/0! | #DIV/0! | #DIV/0! | #DIV/0! | #DIV/0! | #DIV/0! | #DIV/0! | #DIV/0! | #DIV/0! | #DIV/0! | #DIV/0! | #DIV/0! | #DIV/0! | #DIV/0! | #DIV/0! | #DIV/0! | #DIV/0! | #DIV/0! | #DIV/0! | #DIV/0! | #DIV/0!
Money You Invested (+) | #DIV/0! | #DIV/0! | #DIV/0! | #DIV/0! | #DIV/0! | #DIV/0! | #DIV/0! | #DIV/0! | #DIV/0! | #DIV/0! | #DIV/0! | #DIV/0! | #DIV/0! | #DIV/0! | #DIV/0! | #DIV/0! | #DIV/0! | #DIV/0! | #DIV/0! | #DIV/0! | #DIV/0! | #DIV/0! | #DIV/0! | #DIV/0! | #DIV/0! | #DIV/0! | #DIV/0! | #DIV/0! | #DIV/0! | #DIV/0! | #DIV/0! | #DIV/0! | #DIV/0! | #DIV/0! | #DIV/0! | #DIV/0!
Money You Invested (-) | #DIV/0! | #DIV/0! | #DIV/0! | #DIV/0! | #DIV/0! | #DIV/0! | #DIV/0! | #DIV/0! | #DIV/0! | #DIV/0! | #DIV/0! | #DIV/0! | #DIV/0! | #DIV/0! | #DIV/0! | #DIV/0! | #DIV/0! | #DIV/0! | #DIV/0! | #DIV/0! | #DIV/0! | #DIV/0! | #DIV/0! | #DIV/0! | #DIV/0! | #DIV/0! | #DIV/0! | #DIV/0! | #DIV/0! | #DIV/0! | #DIV/0! | #DIV/0! | #DIV/0! | #DIV/0! | #DIV/0! | #DIV/0!
Revenue | 0.00 | 0.00 | 0.00 | 0.00 | 0.00 | 0.00 | 0.00 | 0.00 | 0.00 | 0.00 | 0.00 | 0.00 | 0.00 | 0.00 | 0.00 | 0.00 | 0.00 | 0.00 | 0.00 | 0.00 | 0.00 | 0.00 | 0.00 | 0.00 | 0.00 | 0.00 | 0.00 | 0.00 | 0.00 | 0.00 | 0.00 | 0.00 | 0.00 | 0.00 | 0.00 | 0.00
Variable Cost | 0.00 | 0.00 | 0.00 | 0.00 | 0.00 | 0.00 | 0.00 | 0.00 | 0.00 | 0.00 | 0.00 | 0.00 | 0.00 | 0.00 | 0.00 | 0.00 | 0.00 | 0.00 | 0.00 | 0.00 | 0.00 | 0.00 | 0.00 | 0.00 | 0.00 | 0.00 | 0.00 | 0.00 | 0.00 | 0.00 | 0.00 | 0.00 | 0.00 | 0.00 | 0.00 | 0.00
Fixed Cost | #DIV/0! | #DIV/0! | #DIV/0! | #DIV/0! | #DIV/0! | #DIV/0! | #DIV/0! | #DIV/0! | #DIV/0! | #DIV/0! | #DIV/0! | #DIV/0! | #DIV/0! | #DIV/0! | #DIV/0! | #DIV/0! | #DIV/0! | #DIV/0! | #DIV/0! | #DIV/0! | #DIV/0! | #DIV/0! | #DIV/0! | #DIV/0! | #DIV/0! | #DIV/0! | #DIV/0! | #DIV/0! | #DIV/0! | #DIV/0! | #DIV/0! | #DIV/0! | #DIV/0! | #DIV/0! | #DIV/0! | #DIV/0!
Net Profit | #DIV/0! | #DIV/0! | #DIV/0! | #DIV/0! | #DIV/0! | #DIV/0! | #DIV/0! | #DIV/0! | #DIV/0! | #DIV/0! | #DIV/0! | #DIV/0! | #DIV/0! | #DIV/0! | #DIV/0! | #DIV/0! | #DIV/0! | #DIV/0! | #DIV/0! | #DIV/0! | #DIV/0! | #DIV/0! | #DIV/0! | #DIV/0! | #DIV/0! | #DIV/0! | #DIV/0! | #DIV/0! | #DIV/0! | #DIV/0! | #DIV/0! | #DIV/0! | #DIV/0! | #DIV/0! | #DIV/0! | #DIV/0!

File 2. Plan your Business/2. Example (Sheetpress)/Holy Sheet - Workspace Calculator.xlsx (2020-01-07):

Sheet: Read Me!
Precious Plastic Workspace Calculator
 | Welcome to the Precious Plastic Workspace Calculator! This tool will help you understand the numbers behind starting a Precious Plastic business.
You will learn:
- How much money you need to start your workspace
- How long it will take to pay back your intitial investment
- What prices for your products will cover the costs of production
Before you get started:
1. Only fill in cells that are bordered in blue
2. Get started by clicking on the sales tab below
 |  | Cells where you should enter numbers
 |  | Cells with numbers we calculate for you
 |  | If you click cells with red arrows, more information pops up

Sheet: 1. Sales
Sales
In the first column, list all the products, machines, workshops or services that you plan on selling with your Precious Plastic workspace. In the second column, estimate how much each product or service would cost you in materials. In the third column, estimate the time it will take to create each product or service.
Products or Services | Material Cost for Each Product | Number of Working Hours to Produce Each Product or Service
6 mm Sheet (1m x 1m ) | 14.00 | 0.50
12 mm Sheet (1m x 1m) | 26.00 | 0.75
20 mm Sheet (1m x 1m) | 42.00 | 1.00

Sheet: 2. Costs
Working Hours |  | Investment Costs |  | Fixed Costs
Besides making products & services, you will have to spend time on doing other tasks. In this section, fill in your weekly activities and how many hours you will spend on each activity per week. Do not include the time to directly produce products or services. |  | These are the machines, tools, and other expenses you need to set up your workspace. These costs are also known as your "investment costs" and are only paid once. |  | Fixed costs are the costs that do not vary with the amount of products and services that you produce, but you have to pay on a regular basis. Some costs may need to be paid quarterly or yearly, so do some quick calculations to estimate them on a monthly basis.
Weekly Activities | Hours per Week | Initial Investments | Cost | Fixed Costs | Cost per Month
Sourcing Plastic (Shredder Workspace) | 6.0 | Sheet Press | 7500.00 | Rent | 400.00
Marketing/Social Media/Website | 12.0 | 8 Moulds | 800.00 | Water | 40.00
Sales | 10.0 | Business license and permits | 300.00 | Electricity | 120.00
Administration | 10.0 | Workspace Renovation | 800.00 | Gas | 45.00
Distribution | 6.0 | Tools | 400.00 | Internet | 35.00
Machine Maintenance | 5.0 | Van | 3000.00 | Insurance | 130.00
Cleaning Workspace | 5.0 | Table | 100.00 | Office Snacks | 60.00
 |  | Chairs | 80.00 | Car Insurance/Maintenance/Gas | 90.00
 |  | Coffee Machine | 20.00 | Website Service | 20.00
 |  | First Aid Kit | 50.00 | Office Supplies | 20.00
 |  | Office Supplies | 100.00
 |  | Computer | 250.00
 |  | Speaker | 25.00
 |  | Ventilation System (Fan, Filter and ducting) | 130.00
 |  | Shredded plastic storage shelf | 15.00
 |  | Mould trolley | 12.00
 |  | Sheet storage | 20.00
 |  | Workbench | 25.00
 |  | Scale | 20.00
 |  | Bucket | 5.00
 |  | Scoop | 5.00
 |  | Oiling cloth | 2.00
 |  | Spreading beam | 2.00
 |  | Filter mask | 50.00
 |  | Heat resistant gloves | 15.00
 |  | Work gloves | 8.00
 |  | Boxcutter | 5.00
 |  | Timer | 5.00

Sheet: 3. Dashboard
Dashboard | Sales Overview |  |  |  |  | Wages
 | Products & Services | Selling Price Per Unit | Number of Expected Sales Per Month | Total Product Cost | Profit Margin | Hourly Wage | 12.00
Start by entering your desired hourly wage, selling prices, and expected sales for each product. Then play around with your pricing, hourly wage, and expected sales to see how it affects the time needed to pay back your investment, monthly profit, and monthly pay. Make sure you set prices for your products and services so that the numbers in the profit margin column turn green, which means you are covering the costs of producing them. | 6 mm Sheet (1m x 1m ) | 62.00 | 64.0 | 39.41 | 57.31% |  | 3 | *
 | 12 mm Sheet (1m x 1m) | 83.00 | 60.0 | 64.12 | 29.45%
 | 20 mm Sheet (1m x 1m) | 98.00 | 20.0 | 92.82 | 5.58% | Summary
 |  |  |  |  |  | Money Needed to Start | 21969.84
 |  |  |  |  |  | Months to Pay Back Investment | 10
 |  |  |  |  |  | Full Time Employees Needed | 2.0
 |  |  |  |  |  | Revenue Earned Per Month | 10908.00
 |  |  |  |  |  | Fixed Costs Per Month | 960.00
 |  |  |  |  |  | Material Costs Per Month | 3296.00
 |  |  |  |  |  | Total Wages Paid Per Month | 3969.84
 |  |  |  |  |  | Total Profit Earned Per Month | 2682.16

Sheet: Extras
Extras
This page provides you with some basic finanial statements (Cashflow and Profit & Loss) and shows you the calculations from the previous pages. It's more for those people who want to dive deep into the numbers or provide a bank with forecasted financial statements.
Cash Flow A cash flow analysis shows that you have enough money throughout your first year to buy materials, pay your employees, or make an investment into a new machine.
 | Month 1 | Month 2 | Month 3 | Month 4 | Month 5 | Month 6 | Month 7 | Month 8 | Month 9 | Month 10 | Month 11 | Month 12
Money In Bank (Beginning of Month) | 21969.84 | 13713.84 | 19201.84 | 24689.84 | 30177.84 | 35665.84 | 41153.84 | 46641.84 | 52129.84 | 57617.84 | 63105.84 | 68593.84
Initial Investment | 21969.84
Revenue | 10908.00 | 10908.00 | 10908.00 | 10908.00 | 10908.00 | 10908.00 | 10908.00 | 10908.00 | 10908.00 | 10908.00 | 10908.00 | 10908.00
Total Cash In | 32877.84 | 10908.00 | 10908.00 | 10908.00 | 10908.00 | 10908.00 | 10908.00 | 10908.00 | 10908.00 | 10908.00 | 10908.00 | 10908.00
Investment Costs | -13744.00
Variable Costs | -4460.00 | -4460.00 | -4460.00 | -4460.00 | -4460.00 | -4460.00 | -4460.00 | -4460.00 | -4460.00 | -4460.00 | -4460.00 | -4460.00
Fixed Costs | -960.00 | -960.00 | -960.00 | -960.00 | -960.00 | -960.00 | -960.00 | -960.00 | -960.00 | -960.00 | -960.00 | -960.00
Total Cash Out | -19164.00 | -5420.00 | -5420.00 | -5420.00 | -5420.00 | -5420.00 | -5420.00 | -5420.00 | -5420.00 | -5420.00 | -5420.00 | -5420.00
Net Cashflow | 13713.84 | 5488.00 | 5488.00 | 5488.00 | 5488.00 | 5488.00 | 5488.00 | 5488.00 | 5488.00 | 5488.00 | 5488.00 | 5488.00
Money In Bank (End of Month) | 13713.84 | 19201.84 | 24689.84 | 30177.84 | 35665.84 | 41153.84 | 46641.84 | 52129.84 | 57617.84 | 63105.84 | 68593.84 | 74081.84
Profit and Loss This table is to show how much money the company is projected to make each year. It assumes that you paid yourself for the hours you worked, so the "Net Income" at the bottom is the remaining profit made by your company. It is greatly influenced by the "Monthly Sales Improvement Rate" on the Dashboard page. This table is also useful to show your bank or include in grant applications.
 | Year 1 | Year 2 | Year 3 |  | Yearly Growth Rate
Revenue | 130896.00 | 143985.60 | 158384.16 |  | Low
Cost of Sales | 53520.00 | 58872.00 | 64759.20 |  | 0.10 €
Net Revenue | 77376.00 | 85113.60 | 93624.96
Fixed Costs | 11520.00 | 11520.00 | 11520.00
Gross Income from Operations | 65856.00 | 73593.60 | 82104.96
 |  |  |  |  | Business Tax Rate (Research for your Country)
Business Taxes | 13171.20 | 14718.72 | 16420.99 |  | 20.00%
Net Income | 52684.80 | 58874.88 | 65683.97
Monthly Sales Figures
Products and Services | Revenue | Overhead Cost | Indirect Labor Cost | Production Labor Cost | Material Cost | Total Monthly Cost | Total Monthly Profit | Total Monthly Hours
6 mm Sheet (1m x 1m ) | 3968.00 |  |  |  |  |  | 1445.66 | 32.00
 |  | 316.70 | 925.64 | 384.00 | 896.00 | 2522.34
12 mm Sheet (1m x 1m) | 4980.00 |  |  |  |  |  | 1132.96 | 45.00
 |  | 445.36 | 1301.68 | 540.00 | 1560.00 | 3847.04
20 mm Sheet (1m x 1m) | 1960.00 |  |  |  |  |  | 103.54 | 20.00
 |  | 197.94 | 578.52 | 240.00 | 840.00 | 1856.46
Total Revenue | 10908.00 |  |  |  |  |  | #VALUE!
Total Cost |  | 960.00 | 2805.84 | 1164.00 | 3296.00 | 8225.84 |  | 97.00
Payback Table
Don't worry too much about this one, it's just to make the payback analysis graph on the dashboard | 0 | 0 | 0 | 0 | 0 | 0 | 0 | 0 | 0 | 1 | 1 | 1 | 1 | 1 | 1 | 1 | 1 | 1 | 1 | 1 | 1 | 1 | 1 | 1 | 1 | 1 | 1 | 1 | 1 | 1 | 1 | 1 | 1 | 1 | 1 | 1
Month | 1 | 2 | 3 | 4 | 5 | 6 | 7 | 8 | 9 | 10 | 11 | 12 | 13 | 14 | 15 | 16 | 17 | 18 | 19 | 20 | 21 | 22 | 23 | 24 | 25 | 26 | 27 | 28 | 29 | 30 | 31 | 32 | 33 | 34 | 35 | 36
Money You Invested | -21969.84 | -19287.68 | -16605.52 | -13923.36 | -11241.20 | -8559.04 | -5876.88 | -3194.72 | -512.56 | 2169.60 | 4851.76 | 7533.92 | 10216.08 | 12898.24 | 15580.40 | 18262.56 | 20944.72 | 23626.88 | 26309.04 | 28991.20 | 31673.36 | 34355.52 | 37037.68 | 39719.84 | 42402.00 | 45084.16 | 47766.32 | 50448.48 | 53130.64 | 55812.80 | 58494.96 | 61177.12 | 63859.28 | 66541.44 | 69223.60 | 71905.76
Money You Invested (+) | 0.00 | 0.00 | 0.00 | 0.00 | 0.00 | 0.00 | 0.00 | 0.00 | 0.00 | 2169.60 | 4851.76 | 7533.92 | 10216.08 | 12898.24 | 15580.40 | 18262.56 | 20944.72 | 23626.88 | 26309.04 | 28991.20 | 31673.36 | 34355.52 | 37037.68 | 39719.84 | 42402.00 | 45084.16 | 47766.32 | 50448.48 | 53130.64 | 55812.80 | 58494.96 | 61177.12 | 63859.28 | 66541.44 | 69223.60 | 71905.76
Money You Invested (-) | -21969.84 | -19287.68 | -16605.52 | -13923.36 | -11241.20 | -8559.04 | -5876.88 | -3194.72 | -512.56 | 0.00 | 0.00 | 0.00 | 0.00 | 0.00 | 0.00 | 0.00 | 0.00 | 0.00 | 0.00 | 0.00 | 0.00 | 0.00 | 0.00 | 0.00 | 0.00 | 0.00 | 0.00 | 0.00 | 0.00 | 0.00 | 0.00 | 0.00 | 0.00 | 0.00 | 0.00 | 0.00
Revenue | 10908.00 | 10908.00 | 10908.00 | 10908.00 | 10908.00 | 10908.00 | 10908.00 | 10908.00 | 10908.00 | 10908.00 | 10908.00 | 10908.00 | 10908.00 | 10908.00 | 10908.00 | 10908.00 | 10908.00 | 10908.00 | 10908.00 | 10908.00 | 10908.00 | 10908.00 | 10908.00 | 10908.00 | 10908.00 | 10908.00 | 10908.00 | 10908.00 | 10908.00 | 10908.00 | 10908.00 | 10908.00 | 10908.00 | 10908.00 | 10908.00 | 10908.00
Variable Cost | 4460.00 | 4460.00 | 4460.00 | 4460.00 | 4460.00 | 4460.00 | 4460.00 | 4460.00 | 4460.00 | 4460.00 | 4460.00 | 4460.00 | 4460.00 | 4460.00 | 4460.00 | 4460.00 | 4460.00 | 4460.00 | 4460.00 | 4460.00 | 4460.00 | 4460.00 | 4460.00 | 4460.00 | 4460.00 | 4460.00 | 4460.00 | 4460.00 | 4460.00 | 4460.00 | 4460.00 | 4460.00 | 4460.00 | 4460.00 | 4460.00 | 4460.00
Fixed Cost | 3765.84 | 3765.84 | 3765.84 | 3765.84 | 3765.84 | 3765.84 | 3765.84 | 3765.84 | 3765.84 | 3765.84 | 3765.84 | 3765.84 | 3765.84 | 3765.84 | 3765.84 | 3765.84 | 3765.84 | 3765.84 | 3765.84 | 3765.84 | 3765.84 | 3765.84 | 3765.84 | 3765.84 | 3765.84 | 3765.84 | 3765.84 | 3765.84 | 3765.84 | 3765.84 | 3765.84 | 3765.84 | 3765.84 | 3765.84 | 3765.84 | 3765.84
Net Profit | 2682.16 | 2682.16 | 2682.16 | 2682.16 | 2682.16 | 2682.16 | 2682.16 | 2682.16 | 2682.16 | 2682.16 | 2682.16 | 2682.16 | 2682.16 | 2682.16 | 2682.16 | 2682.16 | 2682.16 | 2682.16 | 2682.16 | 2682.16 | 2682.16 | 2682.16 | 2682.16 | 2682.16 | 2682.16 | 2682.16 | 2682.16 | 2682.16 | 2682.16 | 2682.16 | 2682.16 | 2682.16 | 2682.16 | 2682.16 | 2682.16 | 2682.16

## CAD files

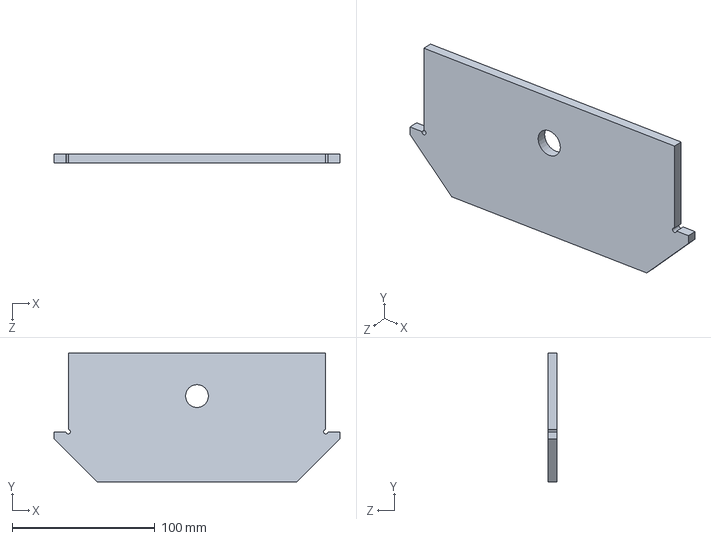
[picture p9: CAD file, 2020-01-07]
3. Build the machine/Upgrades/Sheetpress System/1-3D CAD/Cooling-Press/CoolingPress Solidworks CAD/Jack mount lower^Hotpress asm.sldprt
200.0 x 90.0 x 6.00 mm

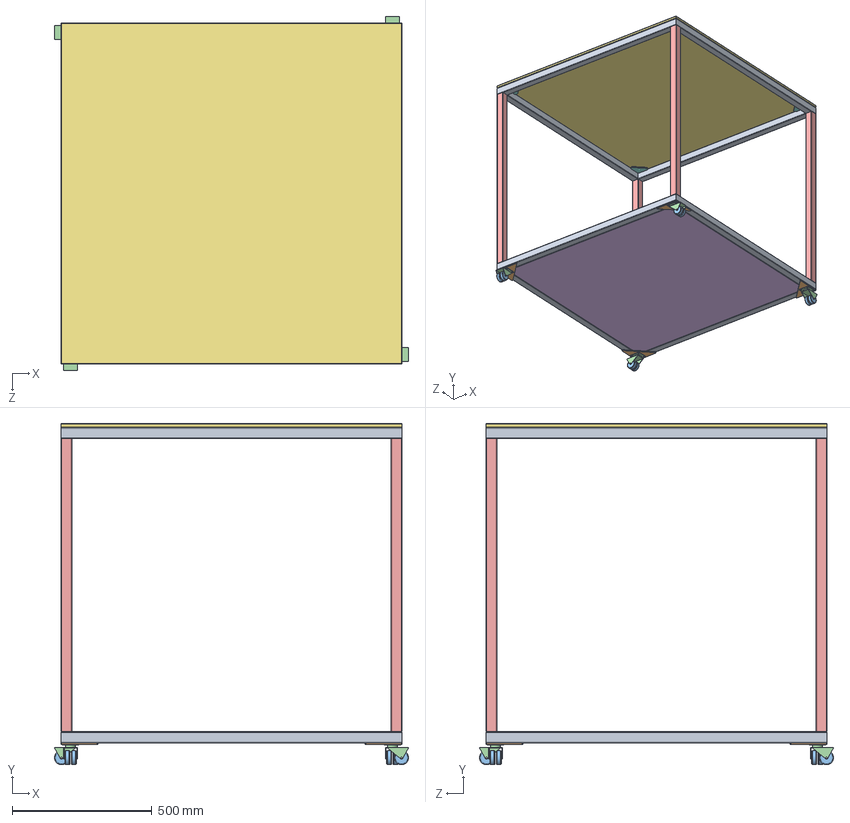
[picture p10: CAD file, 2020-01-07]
3. Build the machine/Upgrades/Sheetpress System/1-3D CAD/Prep-Table/PrepTable Solidworks CAD/PrepTable.SLDASM
1265.0 x 1220.0 x 1265.0 mm
Frame x 2
Wheel mount plate x 4
Wheel x 8

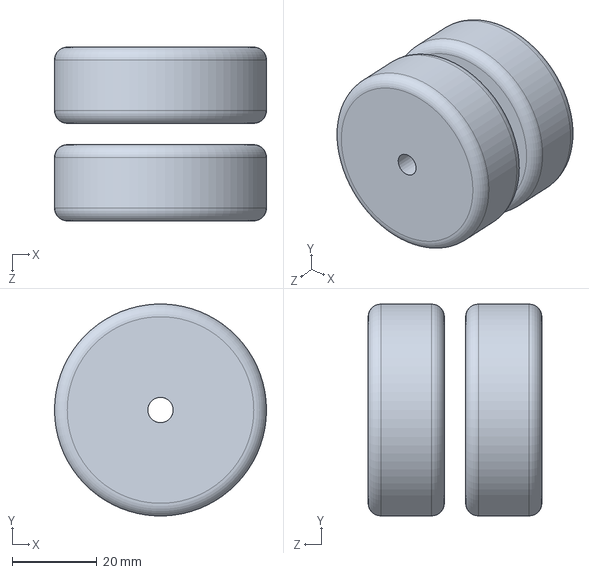
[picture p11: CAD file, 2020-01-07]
3. Build the machine/Upgrades/Sheetpress System/1-3D CAD/Prep-Table/PrepTable Solidworks CAD/Caster wheel.SLDASM
50.0 x 50.0 x 41.0 mm
Wheel x 2

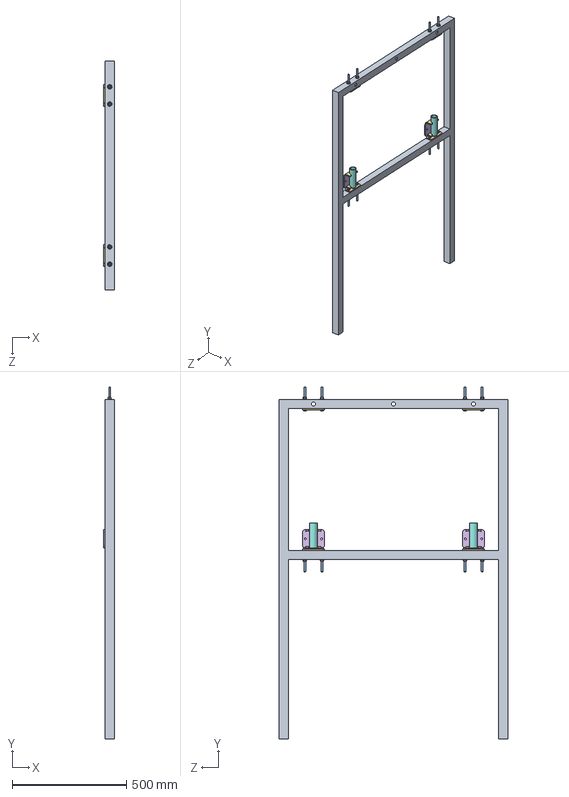
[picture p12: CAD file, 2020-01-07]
3. Build the machine/Upgrades/Sheetpress System/1-3D CAD/Cooling-Press/CoolingPress Solidworks CAD/Side frame asm.sldasm
46.0 x 1539.0 x 1000.0 mm
Side frame
Slider rod plate x 4
hex bolt gradeab_iso x 8
plain washer 10669 type nl_iso x 8
hex nut gradec_iso x 8
Guide plate coldpress x 2
Guide bracket x 2
Slider tube x 2

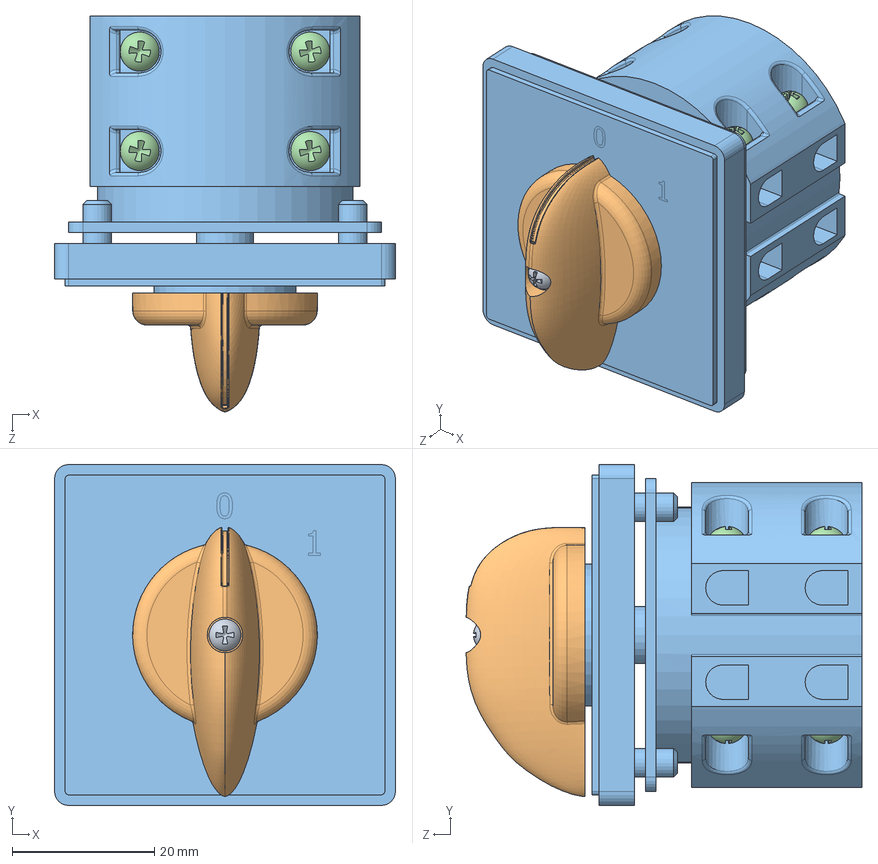
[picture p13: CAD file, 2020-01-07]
3. Build the machine/Sheetpress Files/1-3D CAD/Sheetpress Solidworks CAD/SPR-V1 5000.00-A Rotary Switch.SLDASM
48.0 x 48.0 x 55.7 mm
Винт A2 ГОСТ 17473-80 M2.5-6gx10.stp
Iek ПКП - 10 0_1.stp
Корпус.stp
Винт A2 ГОСТ 17473-80 M3-6gx4.stp x 8

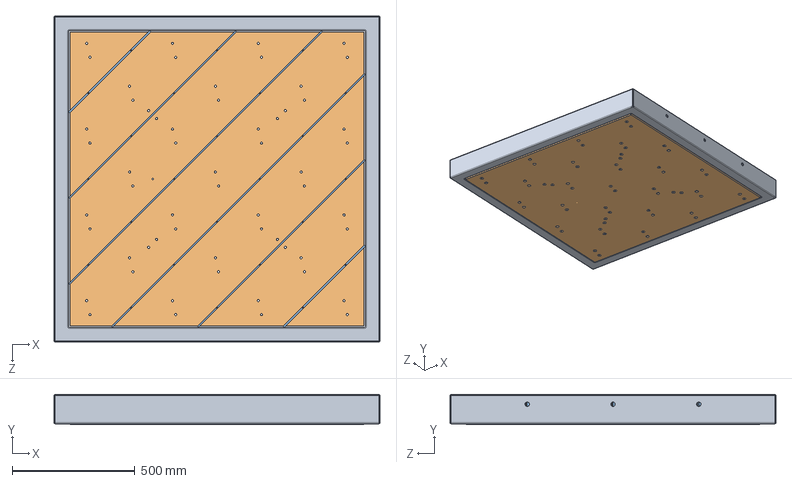
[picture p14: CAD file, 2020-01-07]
3. Build the machine/Sheetpress Files/1-3D CAD/Sheetpress Solidworks CAD/SPR-V1 2000.00-A Pressing plate upper assembly.SLDASM
1330.0 x 123.0 x 1330.0 mm
SPR-V1 2100.01-A Pressing plate frame upper
SPR-V1 2100.02-A Heating plate upper
SPR-V1 2100.03-A Support structure upper B

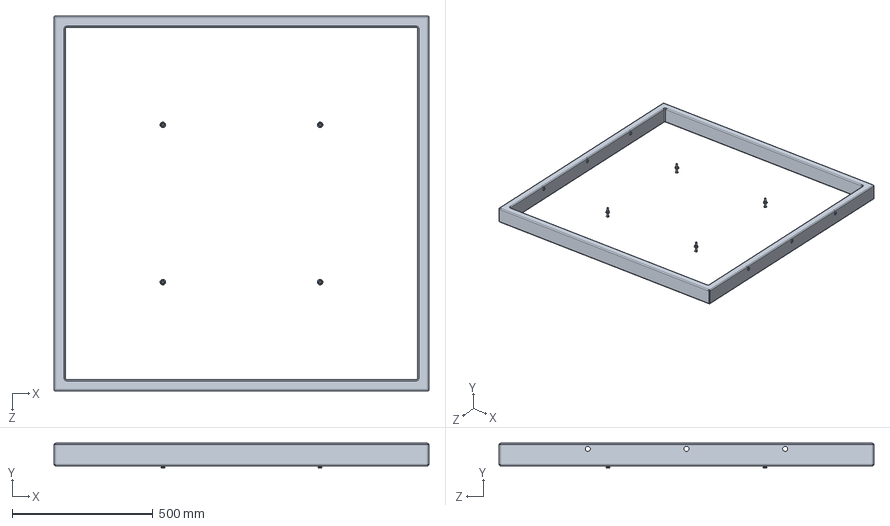
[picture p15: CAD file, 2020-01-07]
3. Build the machine/Upgrades/Sheetpress System/1-3D CAD/Cooling-Press/CoolingPress Solidworks CAD/Pressing plate upper.SLDASM
1330.0 x 87.0 x 1330.0 mm
Plate frame upper
socket countersunk head screw_iso x 4
plain washer 10669 type nl_iso x 4
hex nut gradec_iso x 4

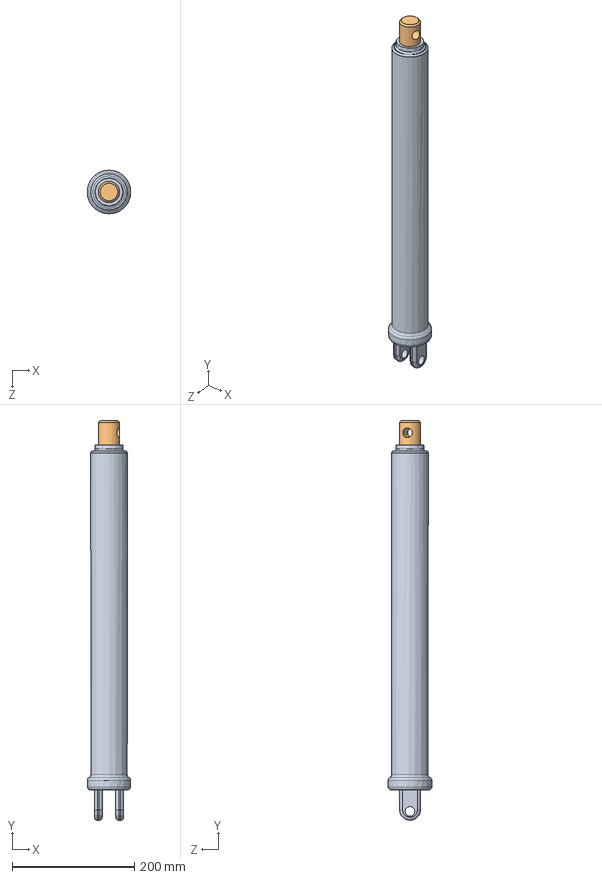
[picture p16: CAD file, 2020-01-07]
3. Build the machine/Upgrades/Sheetpress System/1-3D CAD/Cooling-Press/CoolingPress Solidworks CAD/Jack asm.SLDASM
71.1 x 655.0 x 71.6 mm
Jack rod

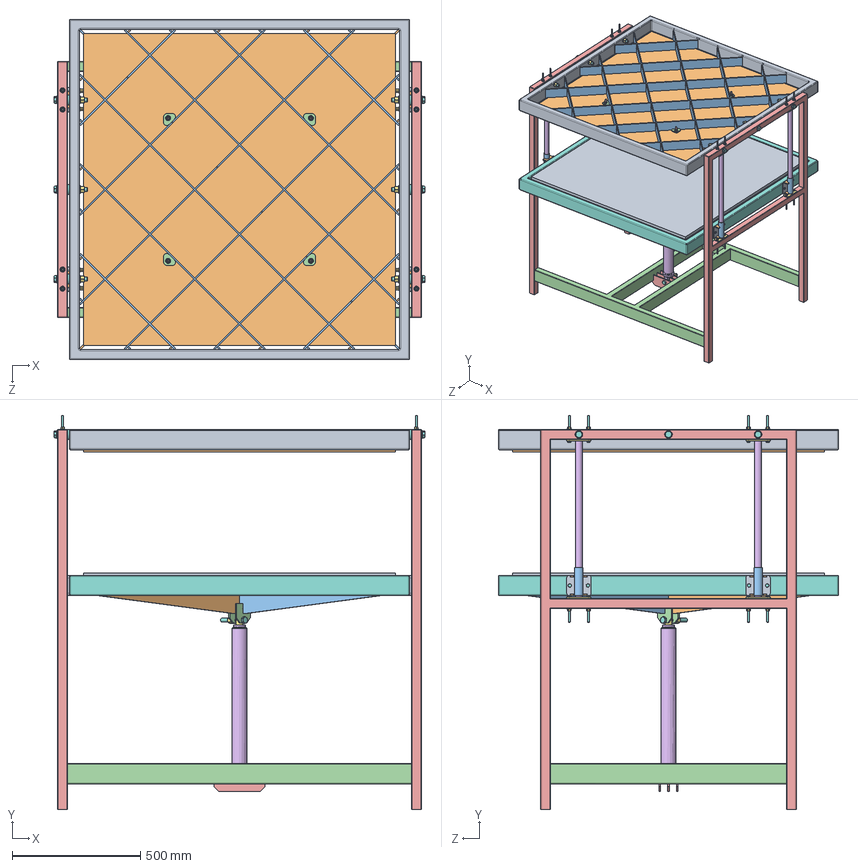
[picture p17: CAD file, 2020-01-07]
3. Build the machine/Upgrades/Sheetpress System/1-3D CAD/Cooling-Press/CoolingPress Solidworks CAD/CoolingPress.SLDASM
1448.0 x 1539.0 x 1330.0 mm
Plate frame upper
Pressing plate upper
Support structure upper x 2
Plywood mount tab x 4
socket countersunk head screw_iso x 4
plain washer 10669 type nl_iso x 28
hex nut gradec_iso x 46
Plate frame lower
Pressing plate lower
Support structure lower a
Support structure lower b
Jack mount x 2
Side frame x 2
Slider rod x 4
Slider rod plate x 8
hex bolt gradeab_iso x 32
Guide plate coldpress x 4
Guide bracket x 4
Slider tube x 4
Jack plate lower x 3
Jack rod
Spacer x 6
plain washer normal grade a_iso x 6
plain washer normal grade c_iso x 6

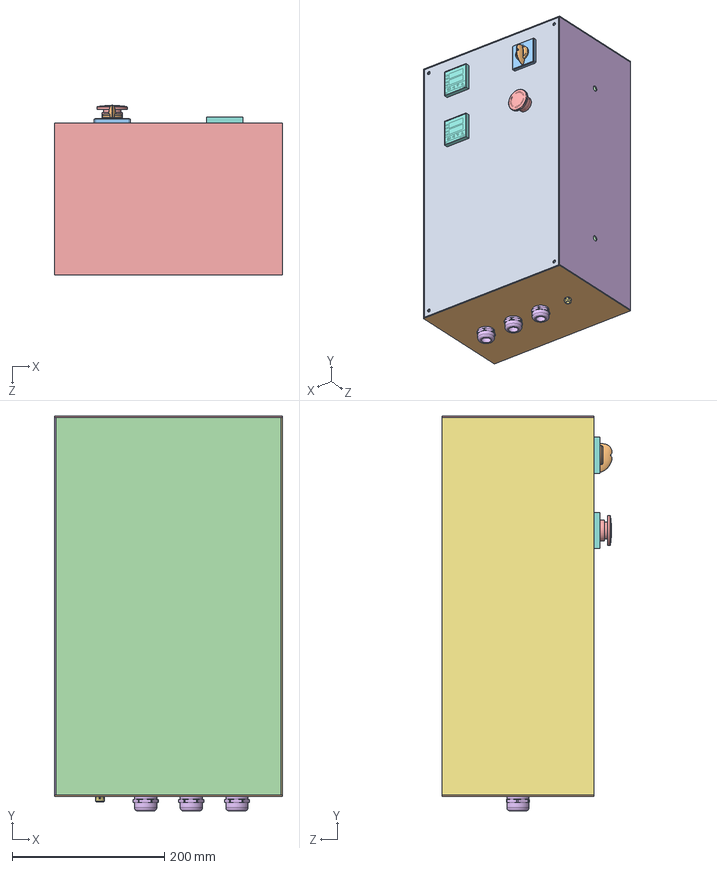
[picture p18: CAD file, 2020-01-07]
3. Build the machine/Sheetpress Files/1-3D CAD/Sheetpress Solidworks CAD/SPR-V1 5000.01-A Electronics Enclosure.SLDASM
300.0 x 519.2 x 223.7 mm
SPR-V1 5000.01-A Electronics Enclosure Front 496x296 2mm Sheet Steel
SPR-V1 5000.01-A Electronics Enclosure Bottom 300x200 2mm Sheet Steel
SPR-V1 5000.02-A-A Electronics Enclosure Front Panel Mount Tab 6mm Sheet Steel M6 x 4
SPR-V1 5000.01-A Electronics Enclosure Back 496x296 2mm Sheet Steel
SPR-V1 5000.01-A Electronics Enclosure Top 300x200 2mm Sheet Steel
SPR-V1 5000.01-A Electronics Enclosure Right 496x200mm Sheet Steel
SPR-V1 5000.01-A Electronics Enclosure Left 496x200mm Sheet Steel
SPR-V1 5000.00-A REX C1000 PID Controler x 2
Винт A2 ГОСТ 17473-80 M2.5-6gx10.stp
Iek ПКП - 10 0_1.stp
Корпус.stp
Винт A2 ГОСТ 17473-80 M3-6gx4.stp x 8
SPR-V1 5000.00-A Emergency Stop
SPR-V1 14 M25 Cable Gland x 3
SPR-V1 16 M10 Gland

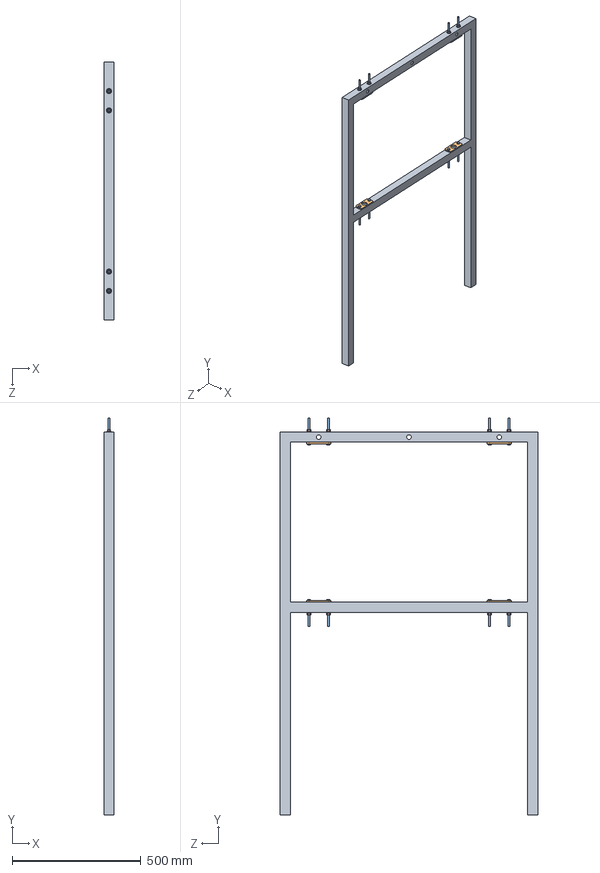
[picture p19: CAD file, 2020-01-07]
3. Build the machine/Upgrades/Sheetpress System/1-3D CAD/Cooling-Press/CoolingPress Solidworks CAD/Side frame sub asm.sldasm
40.0 x 1539.0 x 1000.0 mm
Side frame
Slider rod plate x 4
hex bolt gradeab_iso x 8
plain washer 10669 type nl_iso x 8
hex nut gradec_iso x 8

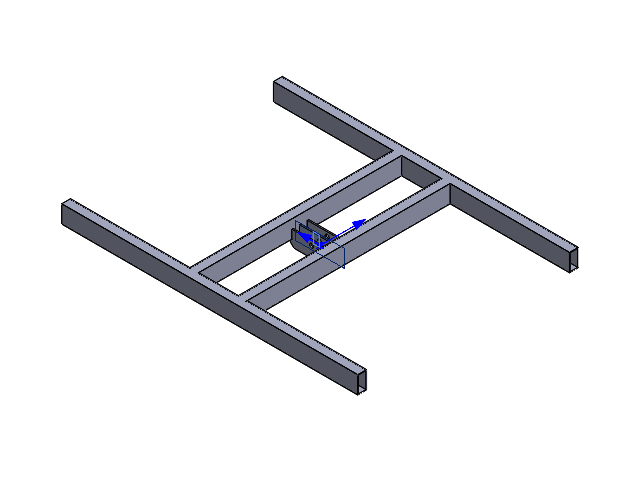
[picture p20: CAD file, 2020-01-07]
3. Build the machine/Upgrades/Sheetpress System/1-3D CAD/Cooling-Press/CoolingPress Solidworks CAD/Bottom frame asm.sldasm
Jack plate lower x 3

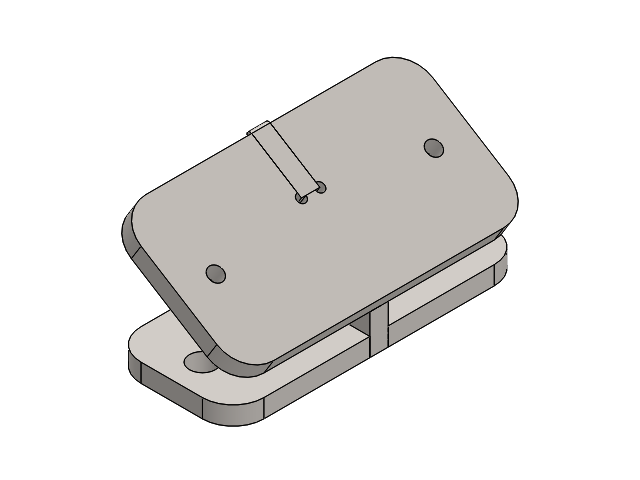
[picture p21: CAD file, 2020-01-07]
3. Build the machine/Sheetpress Files/1-3D CAD/Sheetpress Solidworks CAD/SPR-V1 1000.05-A Hood mounting bracket.sldasm
SPR-V1 1000.05-A Hood bracket 1
SPR-V1 1000.05-A Hood bracket 2
SPR-V1 1000.05-A Hood bracket 3

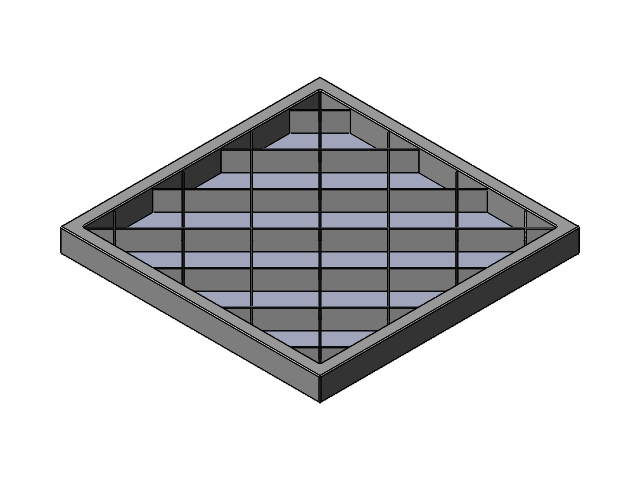
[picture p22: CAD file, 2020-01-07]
3. Build the machine/Upgrades/Sheetpress System/1-3D CAD/Cooling-Press/CoolingPress Solidworks CAD/Pressing plate lower.SLDASM
Plate frame lower
Pressing plate lower
Support structure lower a
Support structure lower b
Jack mount x 2

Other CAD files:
3. Build the machine/Upgrades/Sheetpress System/1-3D CAD/Cooling-Press/CoolingPress Solidworks CAD/Slider bracket.sldasm
3. Build the machine/Upgrades/Sheetpress System/1-3D CAD/Cooling-Press/CoolingPress Solidworks CAD/Support structure upper.sldasm
3. Build the machine/Upgrades/Sheetpress System/1-3D CAD/Cooling-Press/CoolingPress Solidworks CAD/Support structure lower.sldasm
3. Build the machine/Sheetpress Files/1-3D CAD/Sheetpress Solidworks CAD/SPR-V1 4000.00-A Spring assembly.SLDASM
3. Build the machine/Sheetpress Files/1-3D CAD/Sheetpress Solidworks CAD/SPR-V1 0000.01-A Bottom Frame side beams.sldprt
3. Build the machine/Sheetpress Files/1-3D CAD/Sheetpress Solidworks CAD/SPR-V1 0000.01-A Bottom frame jack beams.sldprt
3. Build the machine/Sheetpress Files/1-3D CAD/Sheetpress Solidworks CAD/SPR-V1 0000.01-A Jack mount lower.sldprt
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

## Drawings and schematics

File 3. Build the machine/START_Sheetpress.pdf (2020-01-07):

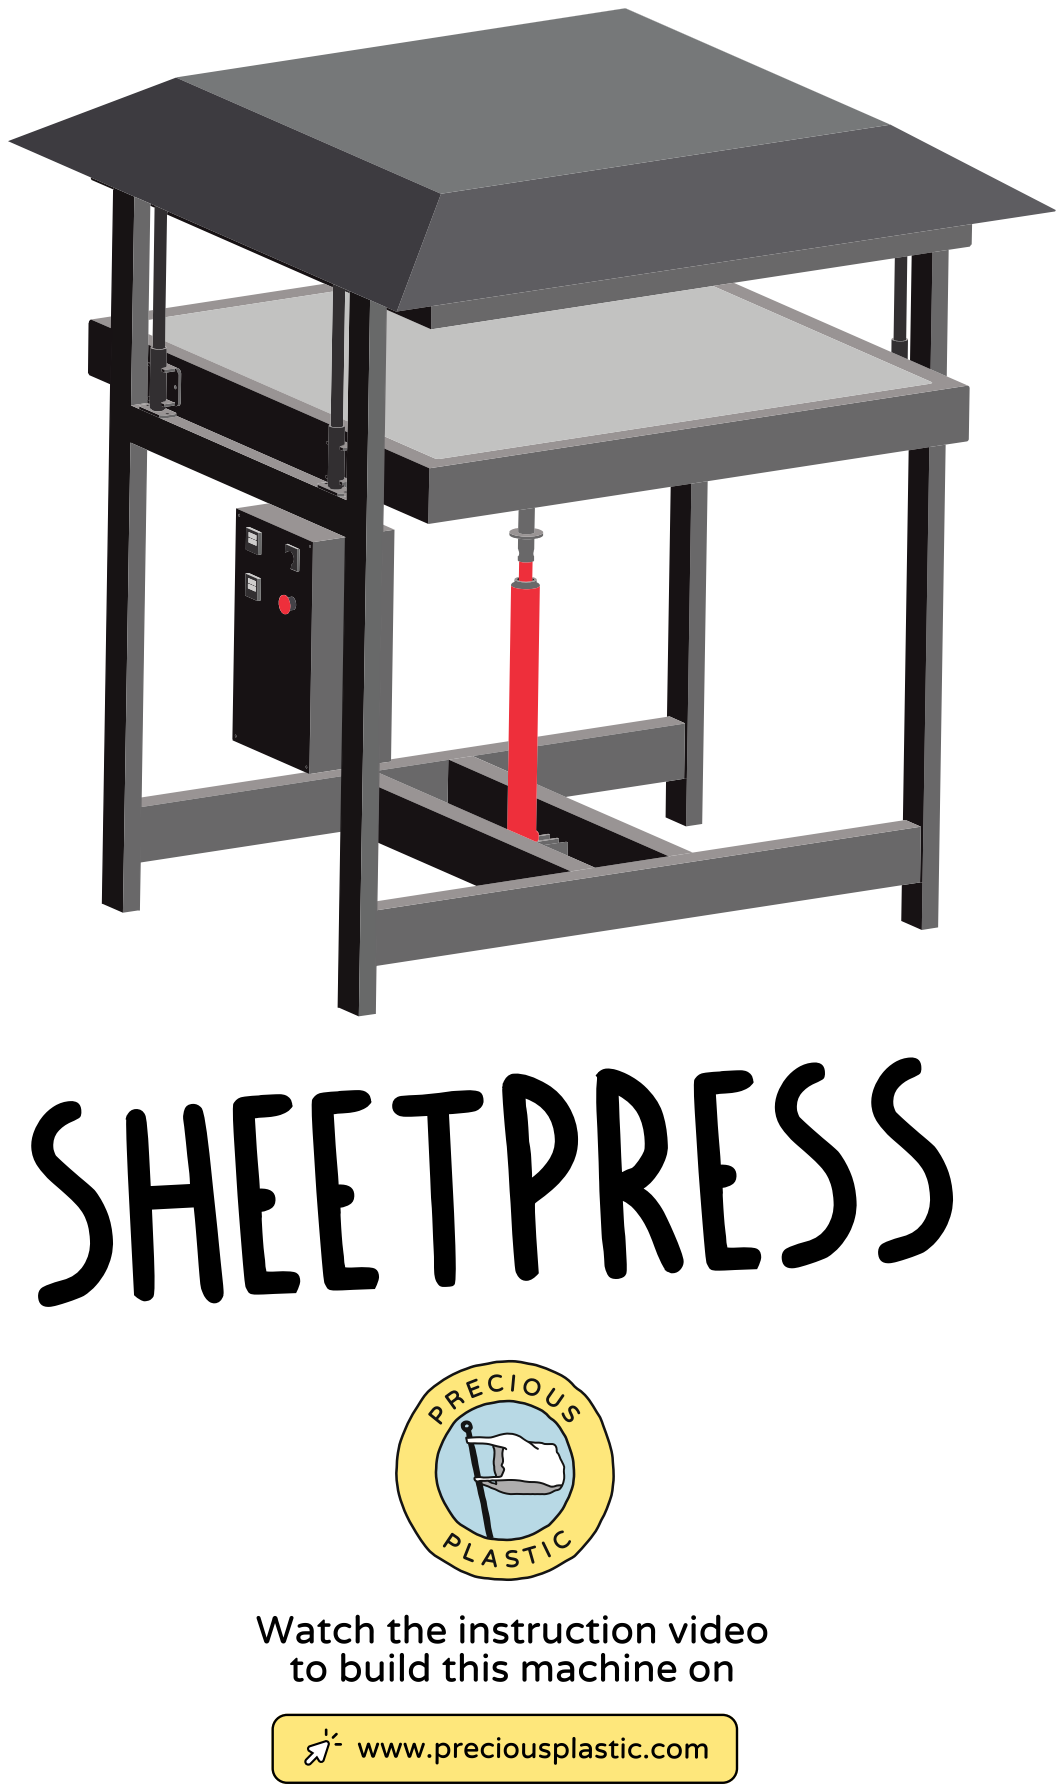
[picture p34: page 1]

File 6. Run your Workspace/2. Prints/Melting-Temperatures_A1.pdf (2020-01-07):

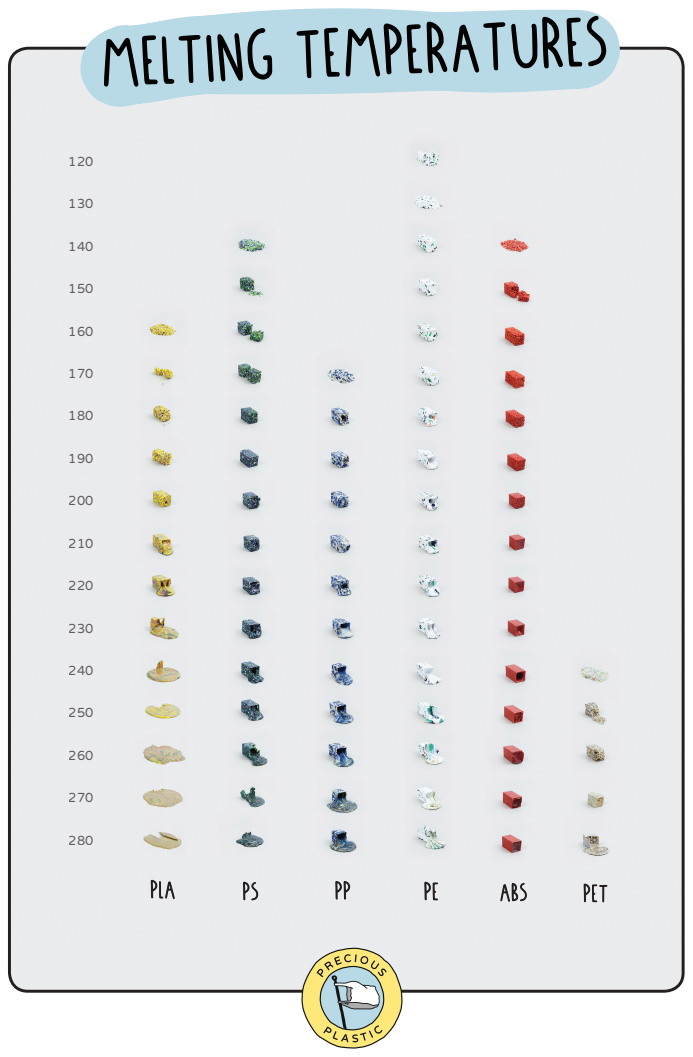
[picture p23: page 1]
melting temperatures; pla; abs; pet

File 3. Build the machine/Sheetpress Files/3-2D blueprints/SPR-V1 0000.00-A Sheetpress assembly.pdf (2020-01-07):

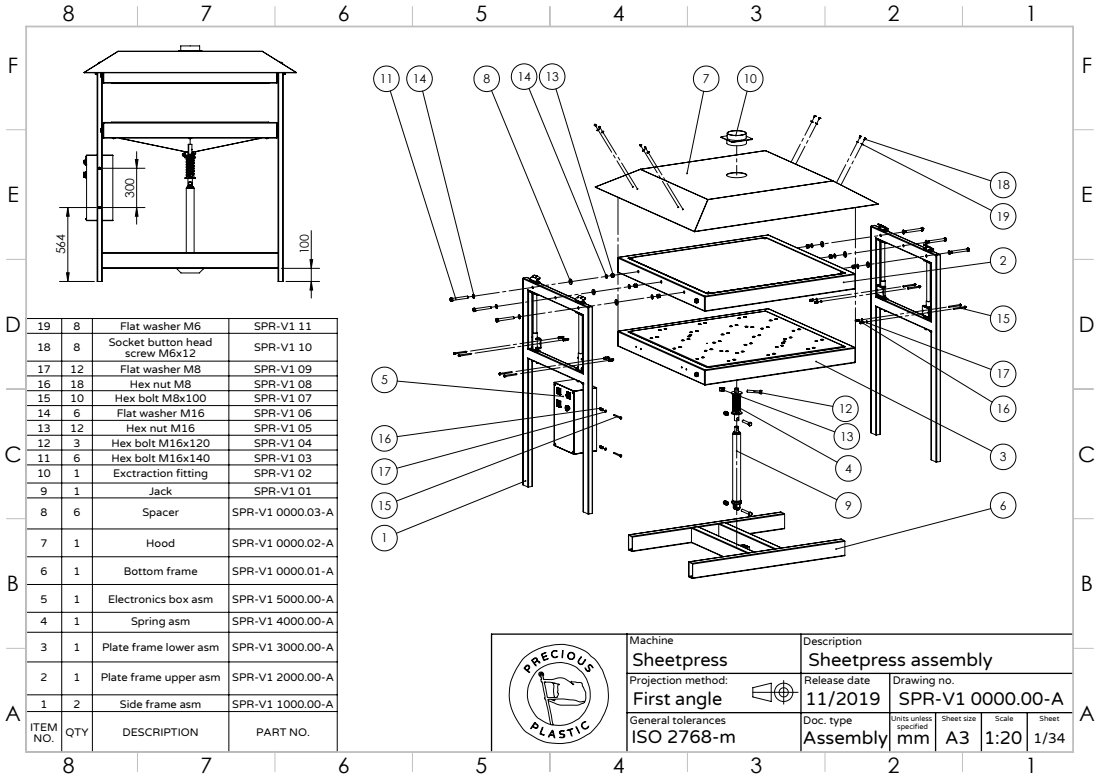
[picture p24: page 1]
Plate frame lower asm; SPR-V1 3000.00-A; QTY; DESCRIPTION; PART NO.; Units unless; ISO 2768-m; General tolerances; Doc. type; Sheet size; Scale; Sheet; Sheetpress assembly

19 | 8 | Flat washer M6 | SPR-V1 11
18 | 8 | Socket button head screw M6x12 | SPR-V1 10
17 | 12 | Flat washer M8 | SPR-V1 09
16 | 18 | Hex nut M8 | SPR-V1 08
15 | 10 | Hex bolt M8x100 | SPR-V1 07
14 | 6 | Flat washer M16 | SPR-V1 06
13 | 12 | Hex nut M16 | SPR-V1 05
12 | 3 | Hex bolt M16x120 | SPR-V1 04
11 | 6 | Hex bolt M16x140 | SPR-V1 03
10 | 1 | Exctraction fitting | SPR-V1 02
9 | 1 | Jack | SPR-V1 01
8 | 6 | Spacer | SPR-V1 0000.03-A

7 | 1 | Hood | SPR-V1 0000.02-A

6 | 1 | Bottom frame | SPR-V1 0000.01-A

5 | 1 | Electronics box asm | SPR-V1 5000.00-A
4 | 1 | Spring asm | SPR-V1 4000.00-A

2 | 1 | Plate frame upper asm | SPR-V1 2000.00-A
1 | 2 | Side frame asm | SPR-V1 1000.00-A

Projection method: First angle | Release date 11/2019 | Drawing no. SPR-V1 0000.00-A

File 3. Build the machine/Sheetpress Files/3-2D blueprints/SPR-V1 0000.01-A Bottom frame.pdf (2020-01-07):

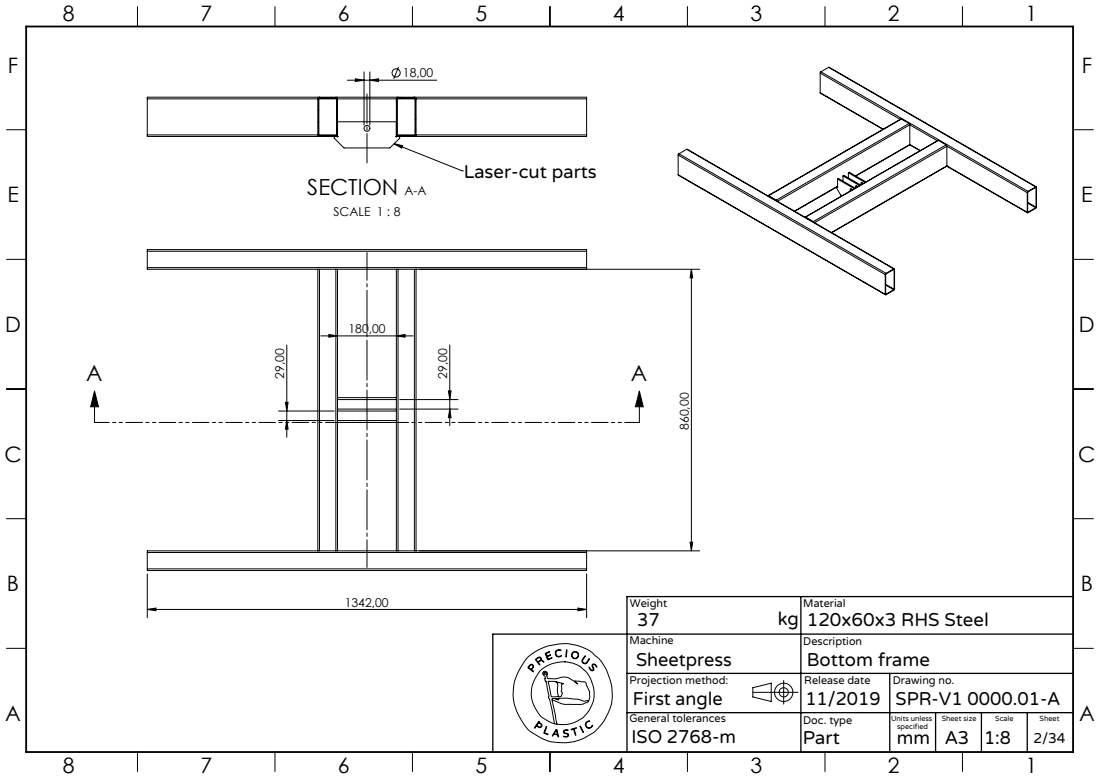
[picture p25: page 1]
SECTION A-A; SCALE 1 : 8

Laser-cut parts

Weight kg 37 | Material 120x60x3 RHS Steel

Machine Sheetpress | Description Bottom frame
Projection method: First angle | Release date 11/2019 | Drawing no. SPR-V1 0000.01-A
General tolerances ISO 2768-m | Doc. type Part | Units unless specified mm | Sheet size A3 | Scale 1:8 | Sheet 2/34

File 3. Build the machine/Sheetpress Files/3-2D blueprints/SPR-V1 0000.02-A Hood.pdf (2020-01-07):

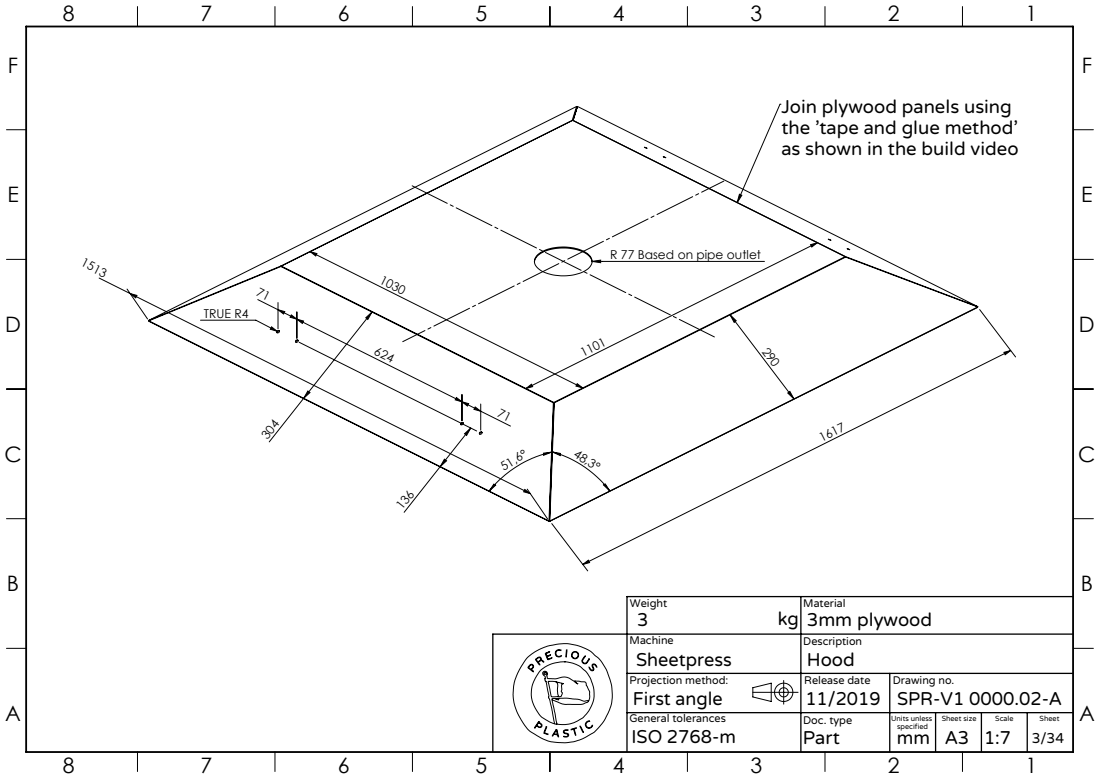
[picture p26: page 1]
TRUE R4

Join plywood panels using
the 'tape and glue method'
as shown in the build video

R 77 Based on pipe outlet

Weight kg 3 | Material 3mm plywood

Machine Sheetpress | Description Hood
Projection method: First angle | Release date 11/2019 | Drawing no. SPR-V1 0000.02-A
General tolerances ISO 2768-m | Doc. type Part | Units unless specified mm | Sheet size A3 | Scale 1:7 | Sheet 3/34

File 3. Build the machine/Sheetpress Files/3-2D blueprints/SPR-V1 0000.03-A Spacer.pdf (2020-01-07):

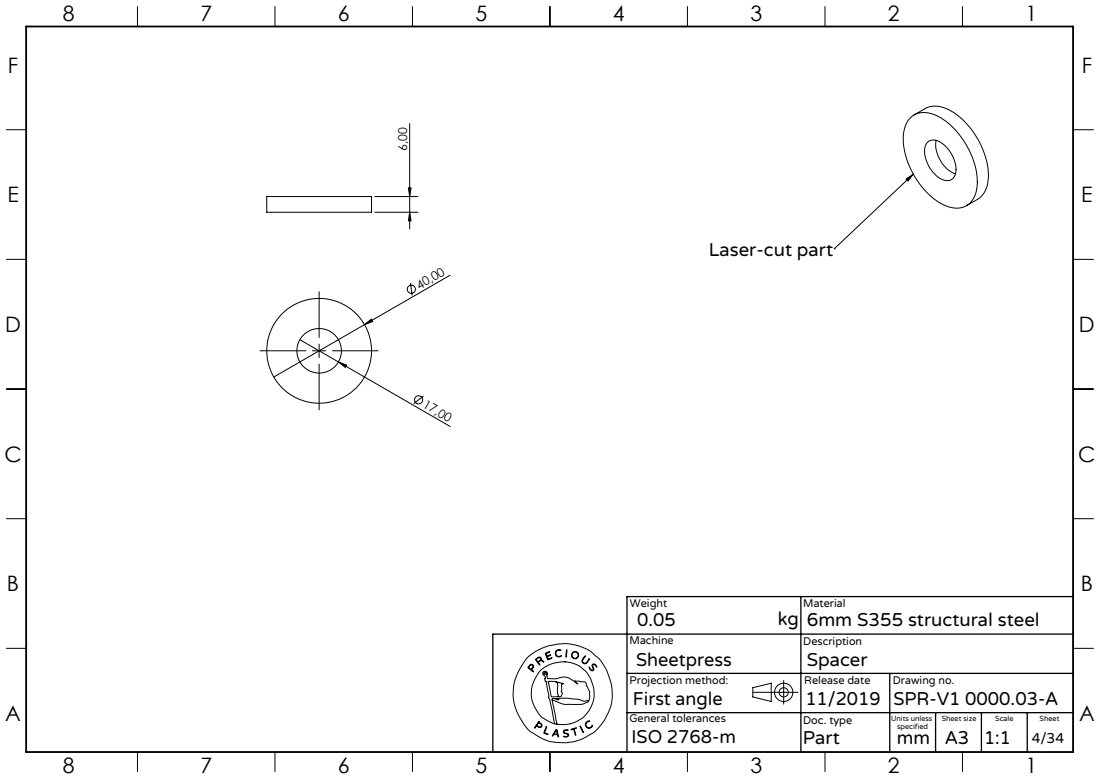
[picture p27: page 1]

Laser-cut part

Weight kg 0.05 | Material 6mm S355 structural steel

Machine Sheetpress | Description Spacer
Projection method: First angle | Release date 11/2019 | Drawing no. SPR-V1 0000.03-A
General tolerances ISO 2768-m | Doc. type Part | Units unless specified mm | Sheet size A3 | Scale 1:1 | Sheet 4/34

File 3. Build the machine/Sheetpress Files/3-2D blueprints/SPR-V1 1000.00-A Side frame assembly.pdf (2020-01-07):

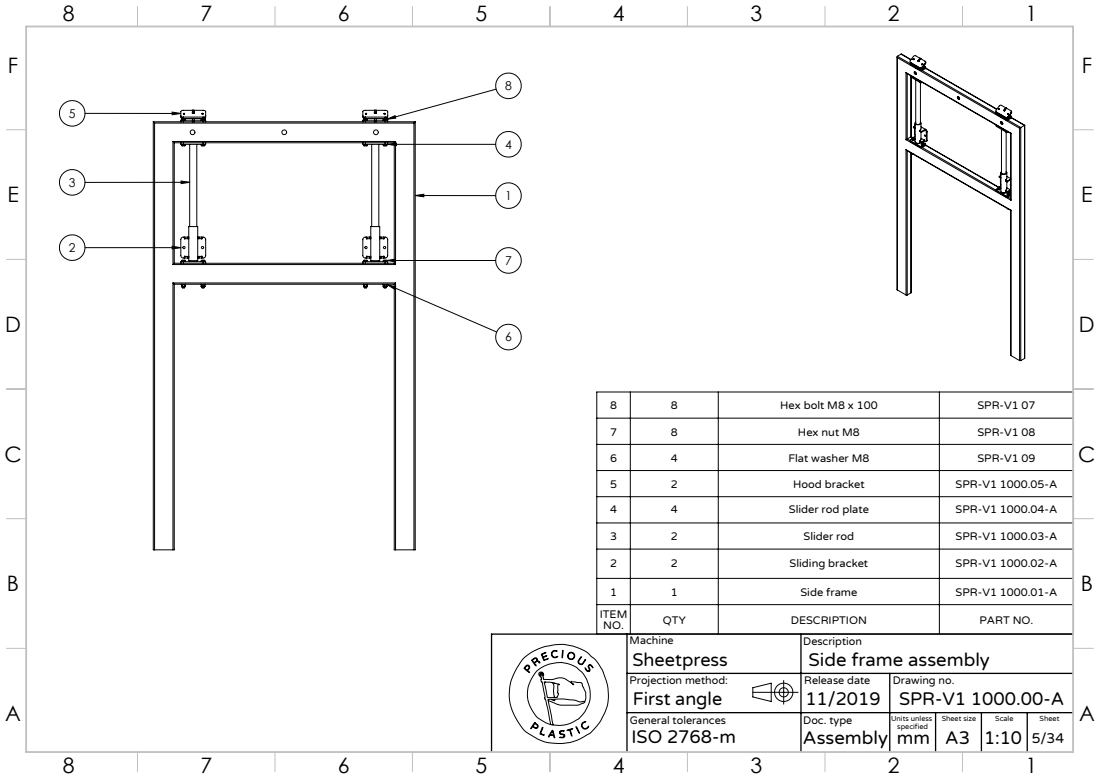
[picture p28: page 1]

8 | 8 | Hex bolt M8 x 100 | SPR-V1 07
7 | 8 | Hex nut M8 | SPR-V1 08
6 | 4 | Flat washer M8 | SPR-V1 09
5 | 2 | Hood bracket | SPR-V1 1000.05-A
4 | 4 | Slider rod plate | SPR-V1 1000.04-A

3 | 2 | Slider rod | SPR-V1 1000.03-A
2 | 2 | Sliding bracket | SPR-V1 1000.02-A

1 | 1 | Side frame | SPR-V1 1000.01-A
ITEM NO. | QTY | DESCRIPTION | PART NO.
Machine Sheetpress | Description Side frame assembly
Projection method: First angle | Release date 11/2019 | Drawing no. SPR-V1 1000.00-A
General tolerances ISO 2768-m | Doc. type Assembly | Units unless specified mm | Sheet size A3 | Scale 1:10 | Sheet 5/34

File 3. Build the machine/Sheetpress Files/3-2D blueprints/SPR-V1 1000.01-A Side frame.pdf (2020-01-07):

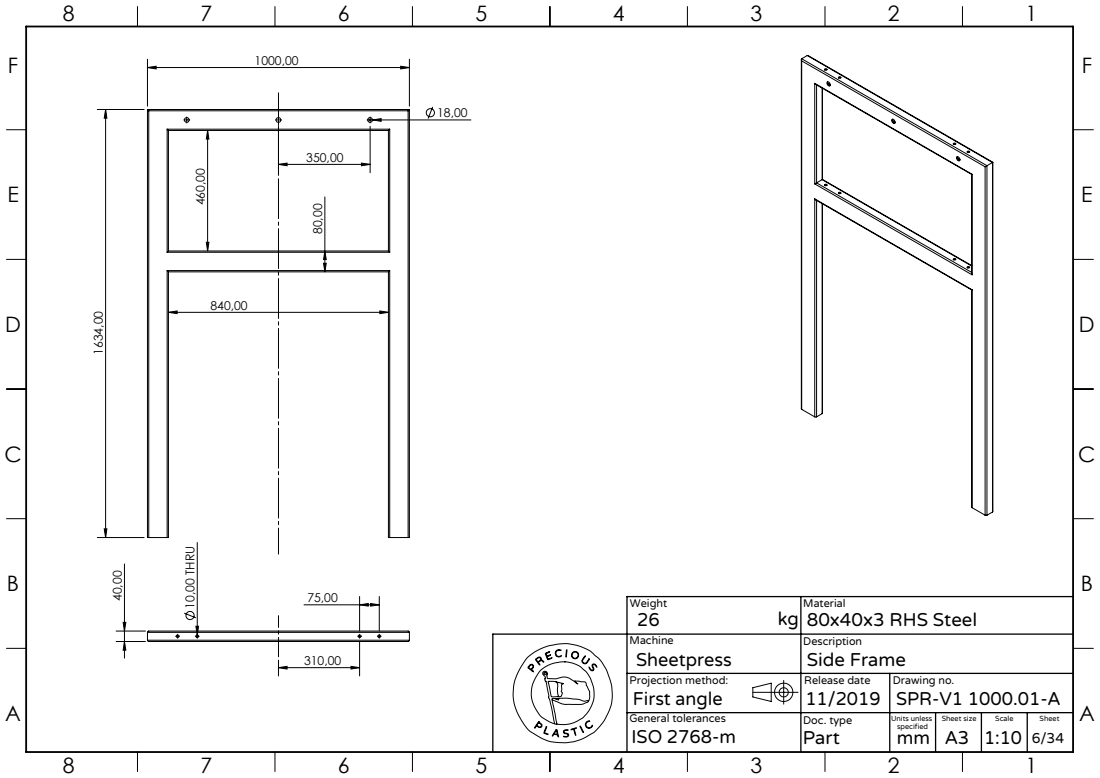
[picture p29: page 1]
10,00 THRU

Weight kg 26 | Material 80x40x3 RHS Steel

Machine Sheetpress | Description Side Frame
Projection method: First angle | Release date 11/2019 | Drawing no. SPR-V1 1000.01-A
General tolerances ISO 2768-m | Doc. type Part | Units unless specified mm | Sheet size A3 | Scale 1:10 | Sheet 6/34

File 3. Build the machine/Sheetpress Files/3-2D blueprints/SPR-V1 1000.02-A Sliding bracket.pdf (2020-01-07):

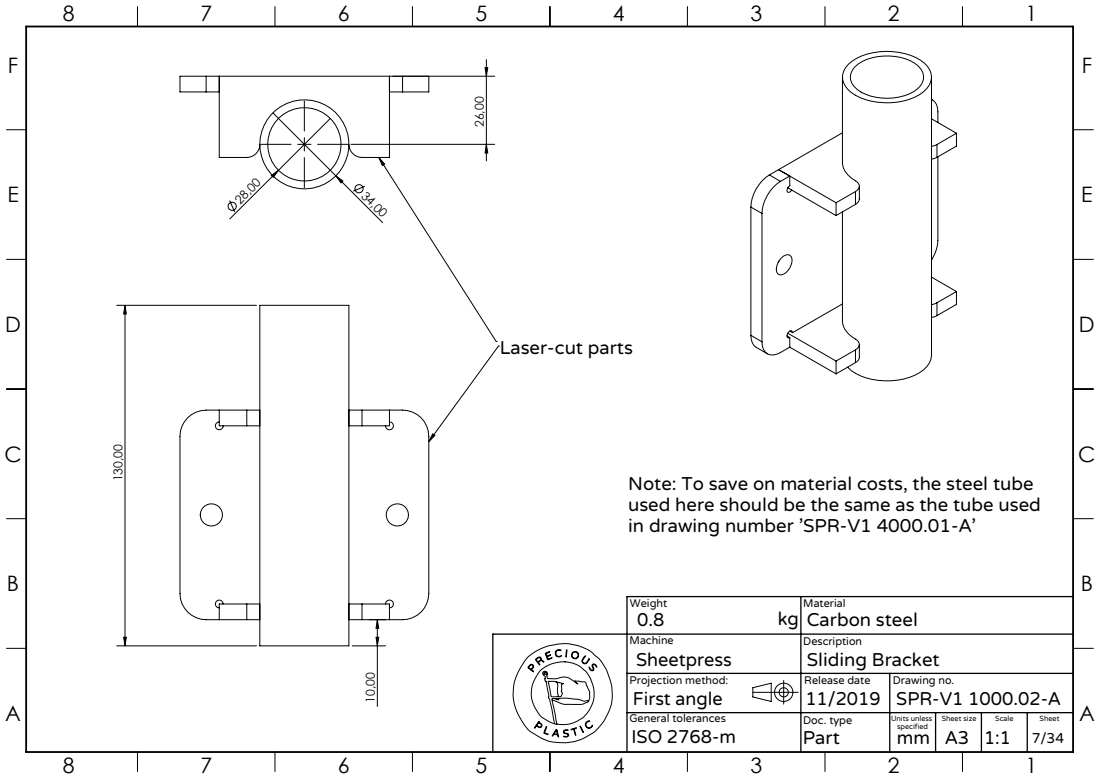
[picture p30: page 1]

Laser-cut parts

Note: To save on material costs, the steel tube
used here should be the same as the tube used
in drawing number 'SPR-V1 4000.01-A'

Weight kg 0.8 | Material Carbon steel

Machine Sheetpress | Description Sliding Bracket
Projection method: First angle | Release date 11/2019 | Drawing no. SPR-V1 1000.02-A
General tolerances ISO 2768-m | Doc. type Part | Units unless specified mm | Sheet size A3 | Scale 1:1 | Sheet 7/34

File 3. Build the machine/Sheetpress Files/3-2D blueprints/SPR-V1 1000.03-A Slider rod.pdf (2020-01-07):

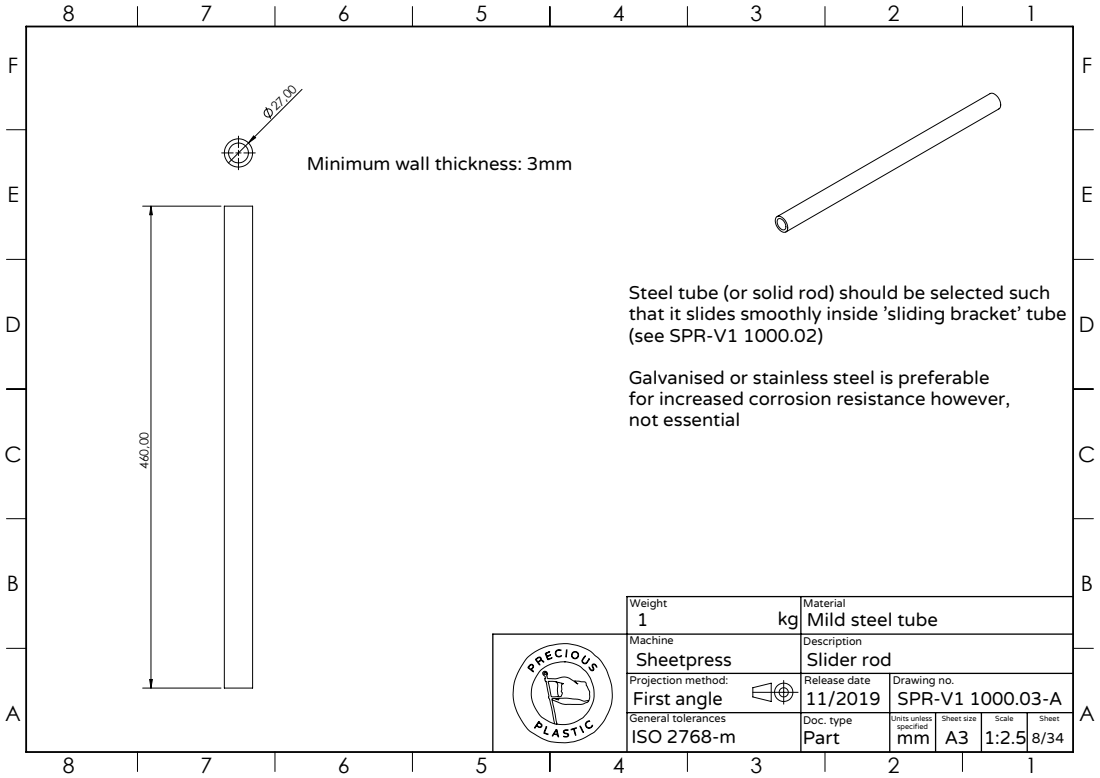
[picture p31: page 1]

Minimum wall thickness: 3mm

Steel tube (or solid rod) should be selected such
that it slides smoothly inside 'sliding bracket' tube
(see SPR-V1 1000.02)

Galvanised or stainless steel is preferable
for increased corrosion resistance however,
not essential

Weight kg 1 | Material Mild steel tube

Machine Sheetpress | Description Slider rod
Projection method: First angle | Release date 11/2019 | Drawing no. SPR-V1 1000.03-A
General tolerances ISO 2768-m | Doc. type Part | Units unless specified mm | Sheet size A3 | Scale 1:2.5 | Sheet 8/34

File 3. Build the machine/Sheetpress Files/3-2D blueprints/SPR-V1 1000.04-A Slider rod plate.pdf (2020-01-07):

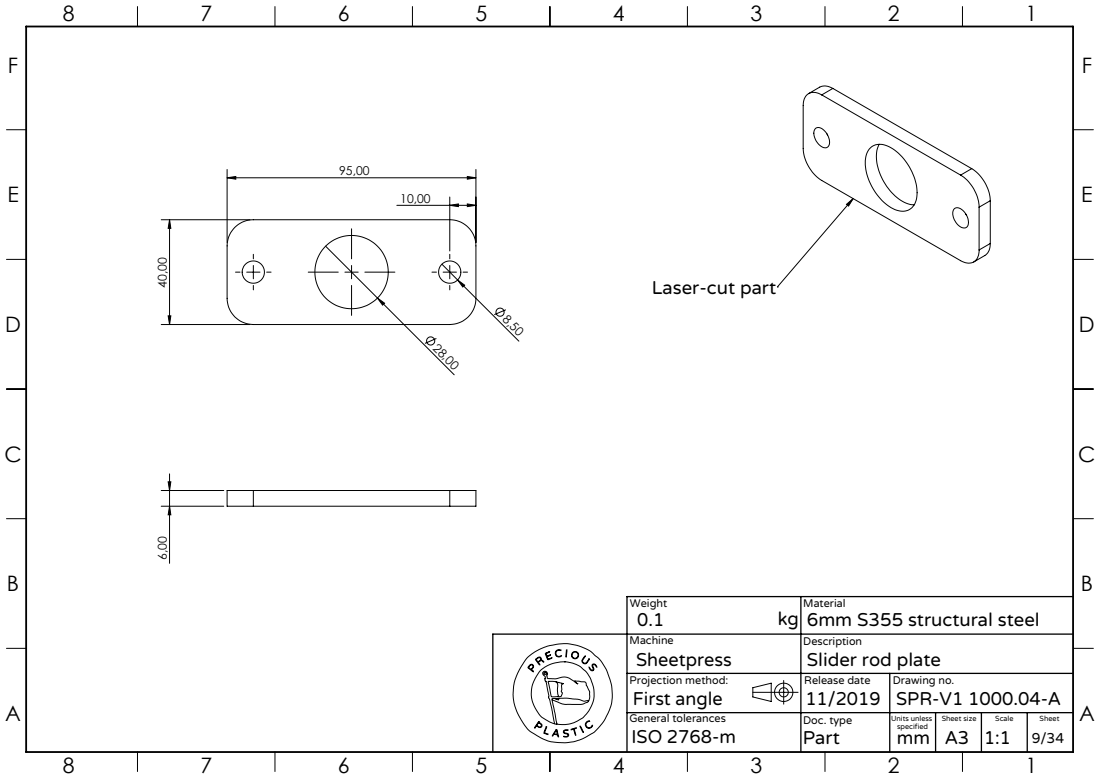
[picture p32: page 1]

Laser-cut part

Weight kg 0.1 | Material 6mm S355 structural steel

Machine Sheetpress | Description Slider rod plate
Projection method: First angle | Release date 11/2019 | Drawing no. SPR-V1 1000.04-A
General tolerances ISO 2768-m | Doc. type Part | Units unless specified mm | Sheet size A3 | Scale 1:1 | Sheet 9/34

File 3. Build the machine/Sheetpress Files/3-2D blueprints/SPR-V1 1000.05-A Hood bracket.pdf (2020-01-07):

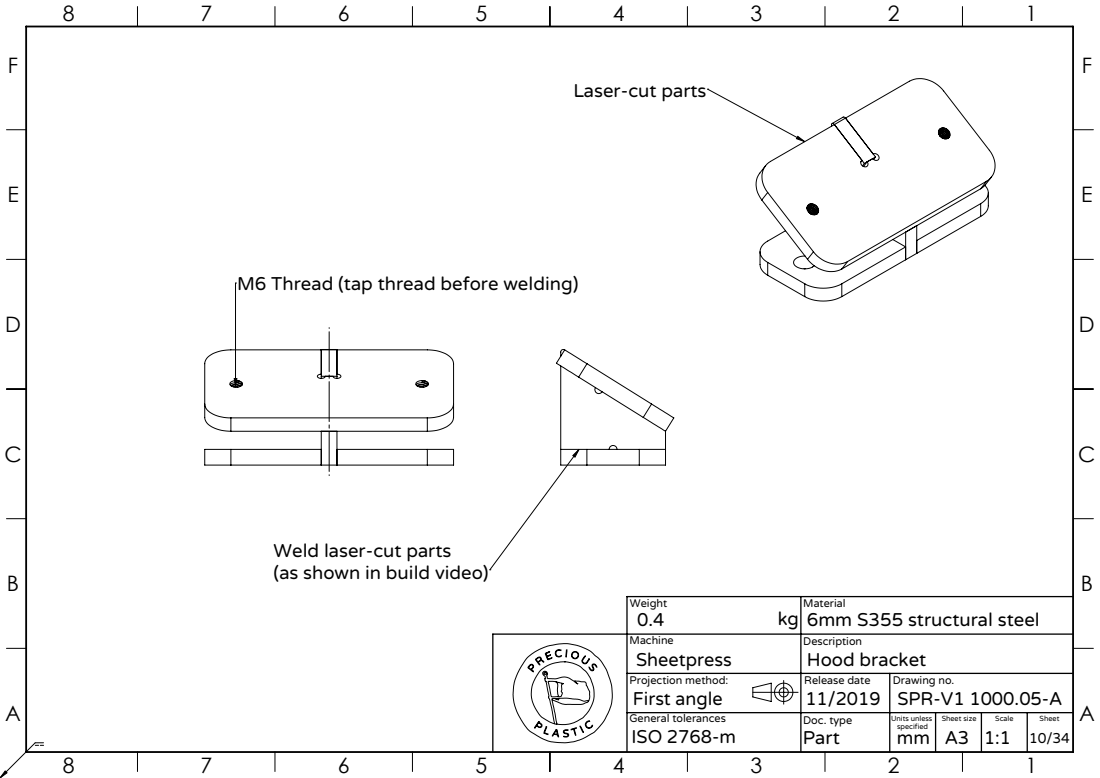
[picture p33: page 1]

Laser-cut parts

M6 Thread (tap thread before welding)

Weld laser-cut parts
(as shown in build video)

Weight kg 0.4 | Material 6mm S355 structural steel

Machine Sheetpress | Description Hood bracket
Projection method: First angle | Release date 11/2019 | Drawing no. SPR-V1 1000.05-A
General tolerances ISO 2768-m | Doc. type Part | Units unless specified mm | Sheet size A3 | Scale 1:1 | Sheet 10/34
